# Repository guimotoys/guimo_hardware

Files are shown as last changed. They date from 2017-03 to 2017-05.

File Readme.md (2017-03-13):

N|Solid (https://guimo.toys)
# [Guimo&trade;] Hardware Sources

## What is Guimo&trade;?
[Guimo&trade;] is a modular smart toy, created to inspire children to live out-of-this-world experiences! It is a being from another planet, who was on an intergallactic mission when was hit by a meteor and fell on the Earth, losing parts of its pieces, programming and personality. The children's goal is to help [Guimo&trade;] recover its programming and mold its personality, by using our free app on a tablet or compatible smartphone.

N|Solid (https://guimo.toys) N|Solid (https://guimo.toys) 

## What is the [Guimo&trade;] Hardware Sources?   

Aqui na pasta de Hardware existe uma lista de todos os componentes necessários para se fazer um Guimo. Essa lista chama-se BOM-Guimo, sinta-se à vontade para baixá-la e adicionar componentes que possam ser compatíveis.

Além disso, há um arquivo com o esquemático da placa do Core. Faça o download e exporte o arquivo da PCB em PDF para posteriormente imprimí-lo e fazer sua própria placa caseira do guimo.
Abaixo segue um tutorial de como fazer sua própria PCB caseira e os materiais necessários:
http://www.robsonmartins.com/eletr/transfterm/

* Observação:
Na hora de fazer a impressão do seu PDF, deve-se atentar-se à orientação da imagem, pois a mesma deve estar invertida como um espelho do circuito final desejado.

## License
Copyright CERN 2013.

This documentation describes Open Hardware and is licensed under the CERN OHL v. 1.2.

You may redistribute and modify this documentation under the terms of the CERN OHL v.1.2. (http://ohwr.org/cernohl). This documentation is distributed WITHOUT ANY EXPRESS OR IMPLIED WARRANTY, INCLUDING OF 
MERCHANTABILITY, SATISFACTORY QUALITY AND FITNESS FOR A PARTICULAR PURPOSE. Please see the CERN OHL v.1.2 for applicable conditions

[Guimo&trade;]: <https://guimo.toys>

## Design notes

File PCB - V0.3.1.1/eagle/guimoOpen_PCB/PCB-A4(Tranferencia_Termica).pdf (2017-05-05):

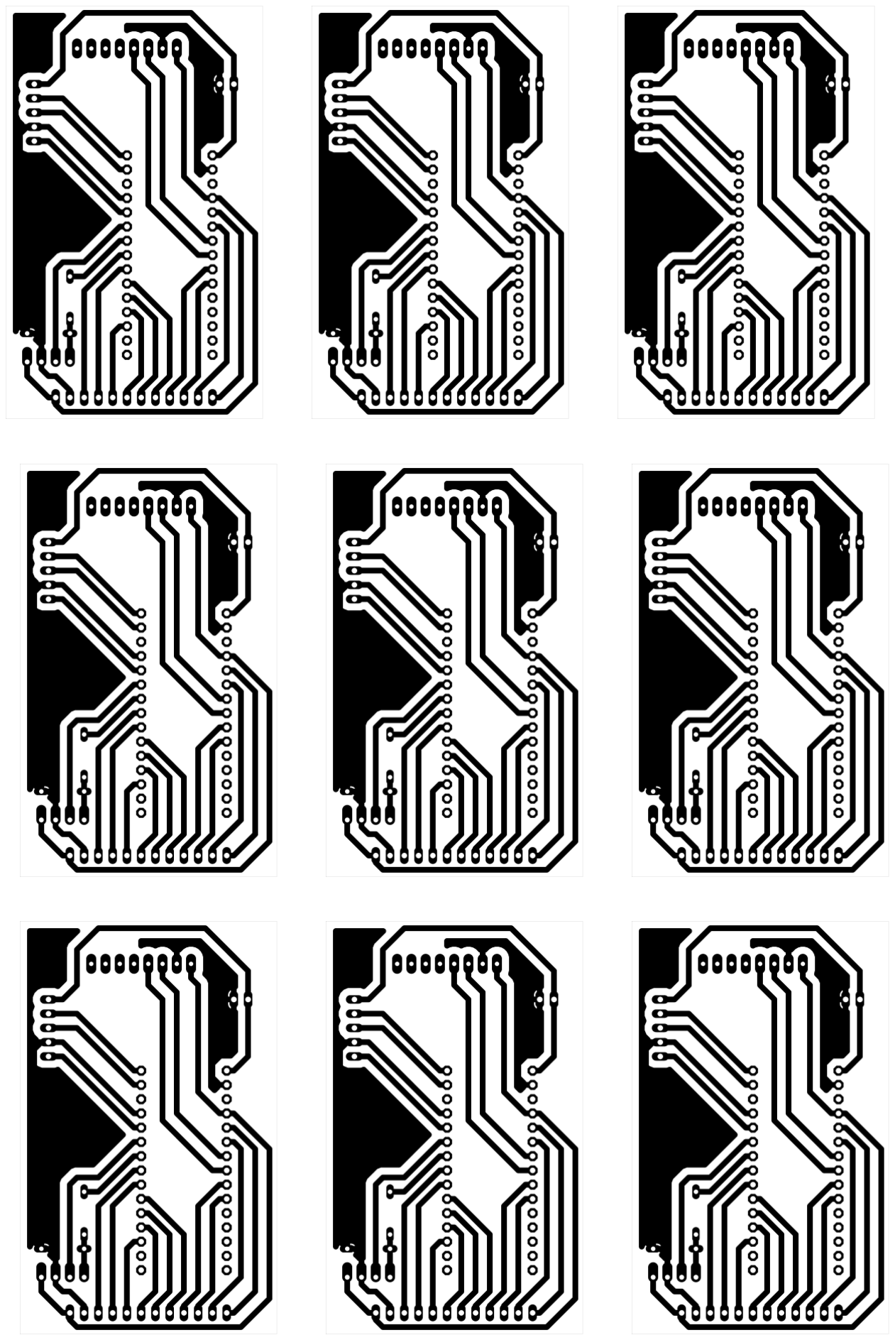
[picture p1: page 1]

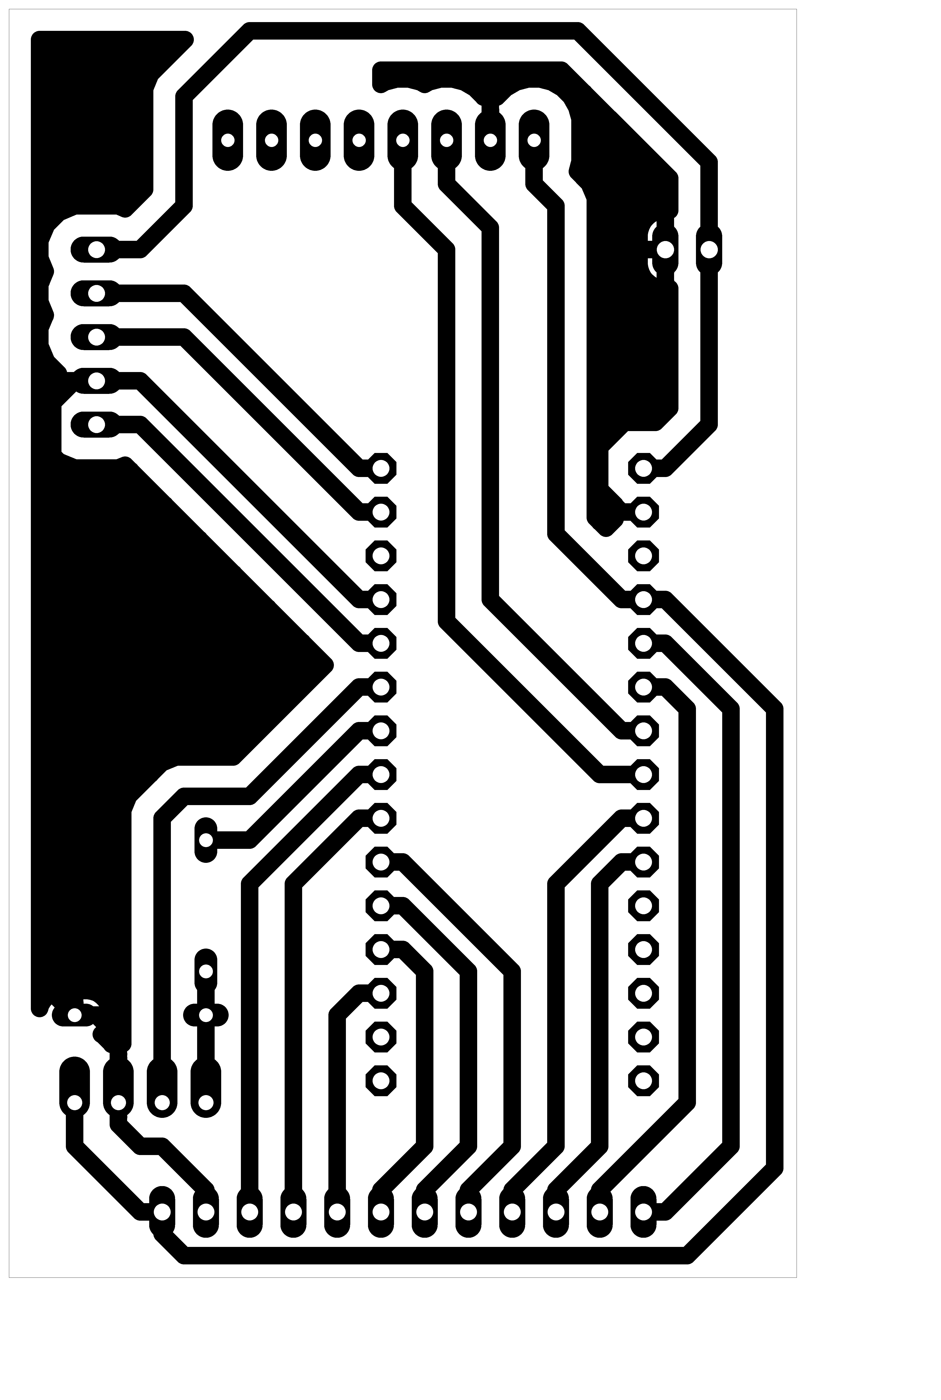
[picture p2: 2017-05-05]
PCB - V0.3.1.1/eagle/guimoOpen_PCB/Fotolito_GuimoV0311(Transferencia_Termica).png

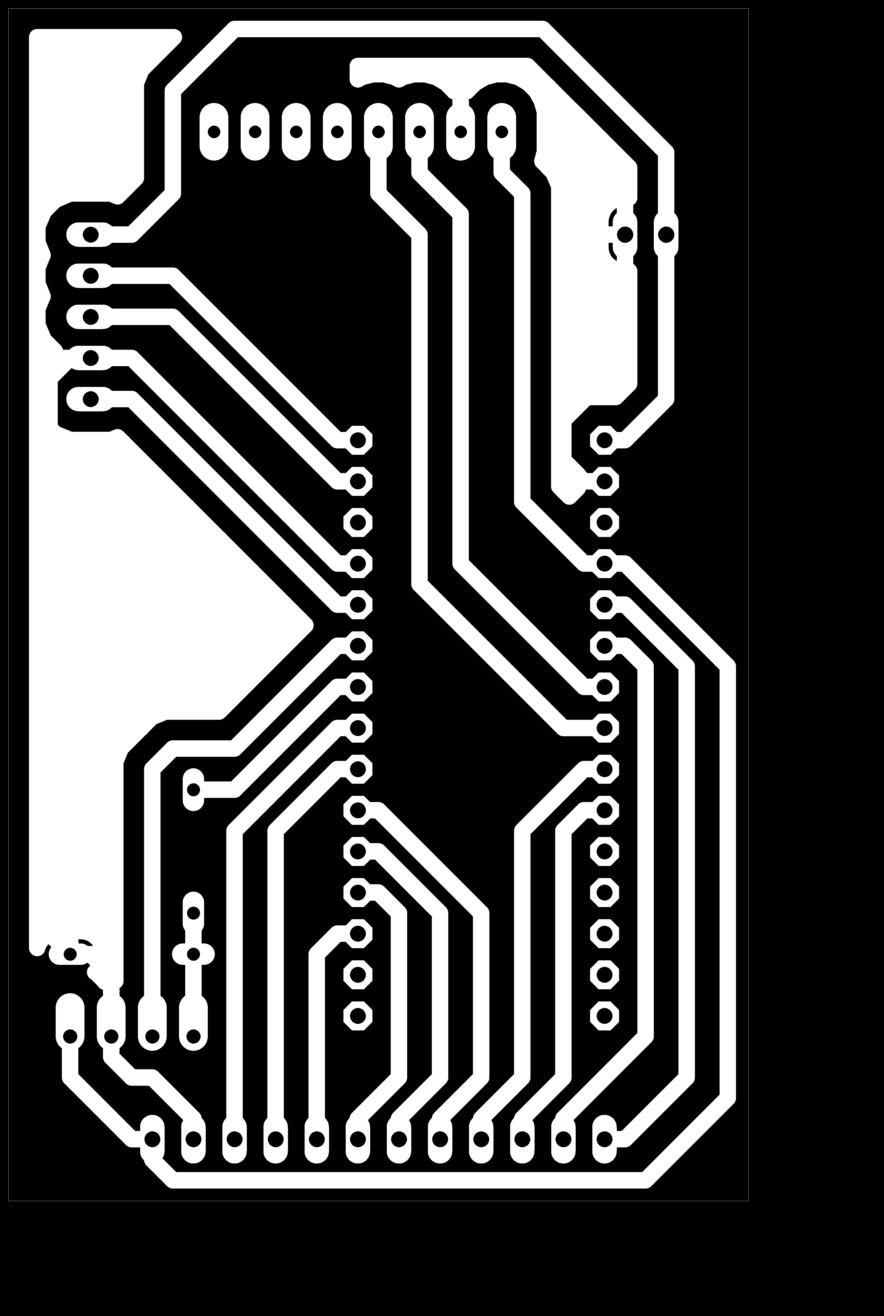
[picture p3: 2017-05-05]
PCB - V0.3.1.1/eagle/guimoOpen_PCB/Fotolito_GuimoV0311(Ultravioleta).png

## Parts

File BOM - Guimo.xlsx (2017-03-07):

 | Quantidade | Código | Nome | Descrição | Fabricante | Número do Fabricante | Preço Unitário (R$) | Preço Total (R$)
Placa Core | 1 | PUR031-C001 | Arduino Nano | ATmega328 Arduino Nano AVR® ATmega MCU 8-Bit AVR Embedded Evaluation Board | Arduino | A000005 | R$49.90 | R$ 49.90
 | 1 | PUR031-C002 | Acelerômetro e Giroscópio | Gy521 Mpu-6050 Module, Axis Gyroscope Module, Accelerometer Module manufacturer / supplier in China, offering Gy-521 Mpu-6050 3 Axis Gyroscope and Accelerometer Module, Wrobot Digital 38kHz IR Transmitter Sensor Arduino Compatible, Serial Port Bluetooth with Baseboardslave Arduino Compatible and so on. | Shanhai | GY521 MPU-6050 Module | R$22.90 | R$ 22.90
 | 1 | PUR031-C003 | Bluetooth | Módulo Bluetooth RS232 HC-05 |  |  | R$36.90 | R$ 36.90
 | 2 | PUR031-C004 | Barra de 15 pinos | 15 Position Header Connector 0.100" (2.54mm) Through Hole Tin | Sullins Connector Solutions | PPTC151LFBN-RC | R$1.09 | R$ 2.18
 | 1 | PUR031-C005 | Barra de 12 pinos | 12 Position Header Connector 0.100" (2.54mm) Through Hole Tin | Sullins Connector Solutions | PPTC121LFBN-RC | R$0.87 | R$ 0.87
 | 1 | PUR031-C006 | Barra de 6 pinos | 6 Position Header Connector 0.100" (2.54mm) Through Hole Tin | Sullins Connector Solutions | PPTC061LFBN-RC | R$0.43 | R$ 0.44
 | 1 | PUR031-C007 | Barra de 5 pinos | 5 Position Header Connector 0.100" (2.54mm) Through Hole Tin | Sullins Connector Solutions | PPTC051LFBN-RC | R$0.36 | R$ 0.36
 | 1 | PUR031-C008 | Barra de 8 pinos | 8 Position Header Connector 0.100" (2.54mm) Through Hole Tin | Sullins Connector Solutions | PPTC081LFBN-RC | R$0.58 | R$ 0.58
 | 1 | PUR031-C009 | Barra de 2 pinos | 2 Positions Header, Breakaway Connector 0.100" (2.54mm) Through Hole Gold | Sullins Connector Solutions | PRPC002SAAN-RC | R$0.07 | R$ 0.07
 | 2 | PUR031-C010 | Resistor | 220 Ohm ±5% 0.25W, 1/4W Through Hole Resistor Axial Flame Retardant Coating, Safety Carbon Film | Stackpole Electronics Inc. | CF14JT220R | R$0.10 | R$ 0.19
Head | 1 | PUR031-H001 | Arduino UNO | ATmega328P Arduino Uno AVR® ATmega MCU 8-Bit AVR Embedded Evaluation Board | Arduino | A000066 | R$49.90 | R$ 49.90
 | 1 | PUR031-H002 | TFT LCD | 2.4'' TFT LCD Shield Arduino ILI9341 | mcufriend | C202 | R$69.90 | R$ 69.90
 | 1 | PUR031-H003 | Cartão Micro SD | Memory Card microSD™ 8GB Class 10 MLC | ATP Electronics, Inc. | AF8GUD3-OEM | R$34.90 | R$ 34.90
 | 1 | PUR031-H004 | Sensor de Toque | Sensor Touch Capacitivo TTP223B |  |  | R$16.90 | R$ 16.90
Body | 2 | PUR031-B001 | Micro Servo Motor | Micro Servo 9g SG90 TowerPro, Peso 9g, Dimensão 23x12.2x29mm, Torque 1.8Kg/cm(4.8V), Tensão de operação: 4.8V, Temperatuda de Operação: 0-55ºC | TowerPro | SG90 | R$14.90 | R$ 29.80

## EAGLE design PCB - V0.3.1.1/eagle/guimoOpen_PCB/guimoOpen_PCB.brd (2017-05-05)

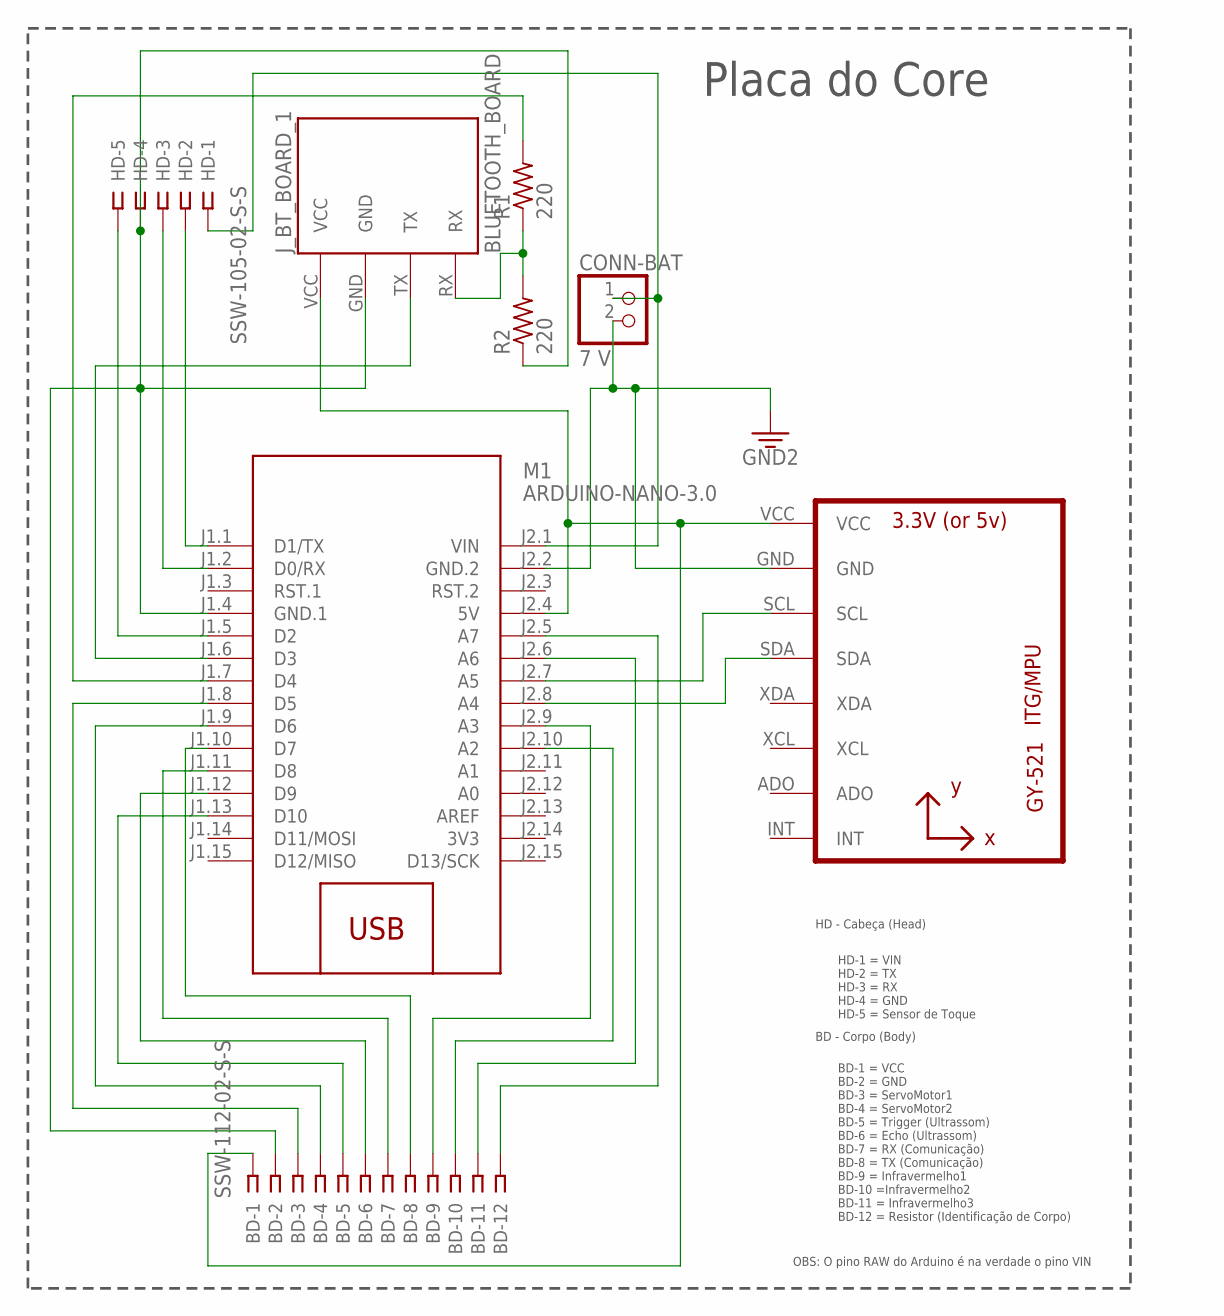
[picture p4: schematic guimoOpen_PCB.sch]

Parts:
BD: SSW-112-02-S-S
CONN-BAT: 7 V; 1X02
HD: SSW-105-02-S-S
J_BT_BOARD_1: BLUETOOTH_BOARD; BT_BOARD_FOOTPRINT
M1: ARDUINO-NANO-3.0
R1, R2: 220; 0207/7
U1: GY-521MPU6050; GY-521

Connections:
3V3: M1.J2.14 (3V3)
GND: BD.2, HD.4, J_BT_BOARD_1.GND, M1.J1.4 (GND.1), R2.1
GND1: CONN-BAT.2, M1.J2.2 (GND.2), U1.GND
unnamed: J_BT_BOARD_1.RX, R1.1, R2.2
unnamed: BD.1, J_BT_BOARD_1.VCC, M1.J2.4 (5V), U1.VCC
unnamed: M1.J2.7 (A5), U1.SCL
unnamed: M1.J2.8 (A4), U1.SDA
unnamed: HD.5, M1.J1.5 (D2)
unnamed: CONN-BAT.1, HD.1, M1.J2.1 (VIN)
unnamed: M1.J1.7 (D4), R1.2
unnamed: BD.4, M1.J1.9 (D6)
unnamed: BD.6, M1.J1.12 (D9)
unnamed: BD.7, M1.J1.11 (D8)
unnamed: BD.5, M1.J1.13 (D10)
unnamed: BD.3, M1.J1.8 (D5)
unnamed: BD.8, M1.J1.10 (D7)
unnamed: BD.12, M1.J2.5 (A7)
unnamed: BD.11, M1.J2.6 (A6)
unnamed: J_BT_BOARD_1.TX, M1.J1.6 (D3)
unnamed: HD.2, M1.J1.1 (D1/TX)
unnamed: BD.9, M1.J2.9 (A3)
unnamed: BD.10, M1.J2.10 (A2)
unnamed: HD.3, M1.J1.2 (D0/RX)

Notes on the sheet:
Placa do Core
BD-1 = VCC BD-2 = GND BD-3 = ServoMotor1 BD-4 = ServoMotor2 BD-5 = Trigger (Ultrassom) BD-6 = Echo (Ultrassom) BD-7 = RX (Comunicação) BD-8 = TX (Comunicação) BD-9 = Infravermelho1 BD-10 =Infravermelho2 BD-11 = Infravermelho3 BD-12 = Resistor (Identificação de Corpo)
HD-1 = VIN HD-2 = TX HD-3 = RX HD-4 = GND HD-5 = Sensor de Toque
HD - Cabeça (Head)
BD - Corpo (Body)
OBS: O pino RAW do Arduino é na verdade o pino VIN

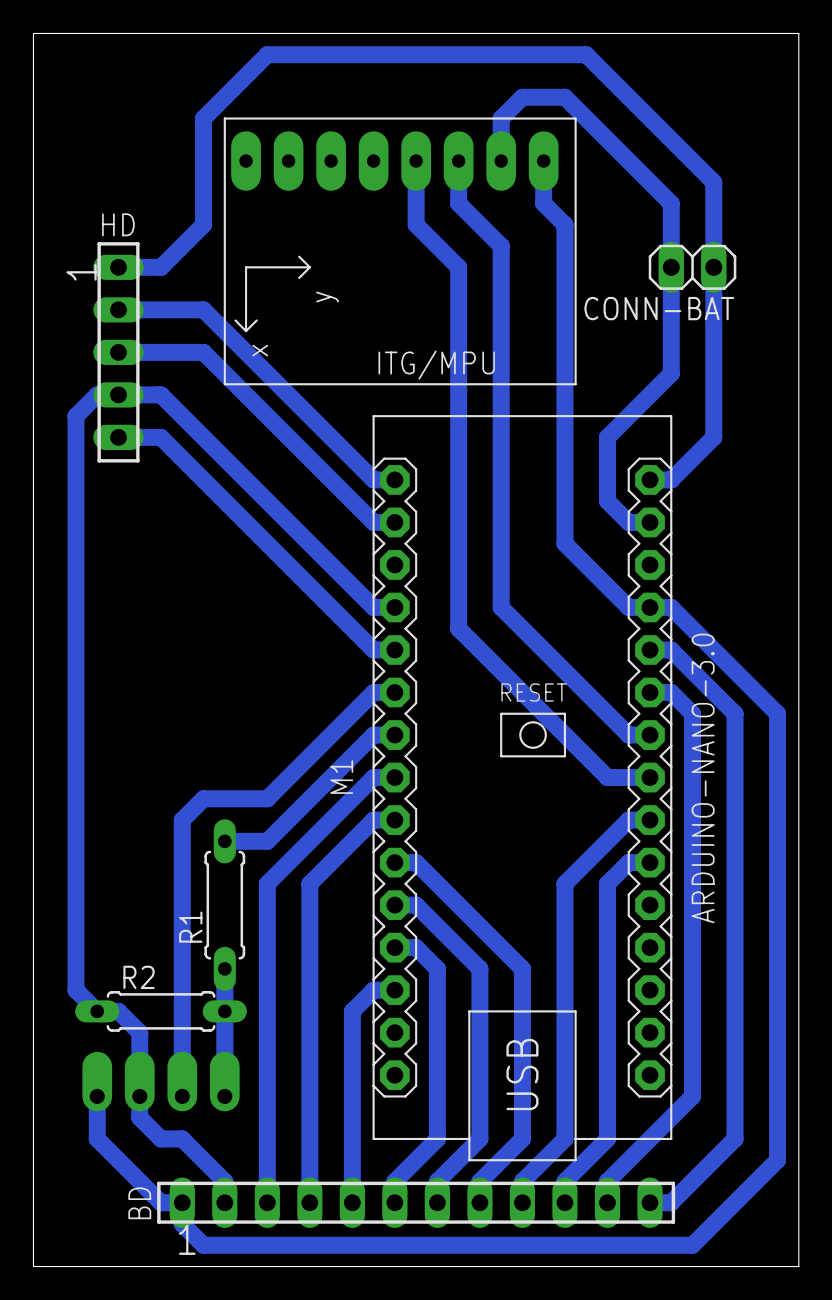
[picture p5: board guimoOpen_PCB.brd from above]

Board: 2 copper layers, 45.7 x 73.7 mm, 8 parts (1 on the bottom side), 22 nets.

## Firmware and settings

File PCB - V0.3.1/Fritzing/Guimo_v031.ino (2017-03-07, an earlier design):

#include <Arduino.h>

// Descrição das Portas Utilizadas
// Digitais: 2,3,5,6,7
// Analógicas: 
// Por Periférico: Ultrassom(D2,D3); Bluetooh(D5,D6); ResistorCorpo(D7); Motores(D10,D11);   

#include <SoftwareSerial.h>
#include<Wire.h>
#include<Servo.h>

#define echoPin 2
#define trigPin 3

char bufB;  //Buffer de comunicação do Bluetooh
char buf;  //Buffer de comunicação com a Cabeça (arduino com arduino)
const int MPU=0x68;  
int AcX,AcY,AcZ; 
int corpo = 7;
int val = 0;
int pinoSensor = A6;
int valorSensor = 0;
long randNumber;

Servo motorDireita, motorEsquerda;

// Define os pinos para a serial  (RX, TX)
SoftwareSerial MinhaSerial(6,5);

void setup() {
  pinMode(trigPin, OUTPUT);
  pinMode(echoPin, INPUT);
  pinMode(corpo, INPUT);

  //Inicia a serial 
  Serial.begin(9600); 
  Serial.println("Dados recebidos :"); 
  
  MinhaSerial.begin(9600);
 
  Wire.begin();
  Wire.beginTransmission(MPU);
  Wire.write(0x6B); 
   
  //Inicializa o MPU-6050
  Wire.write(0); 
  Wire.endTransmission(true);

} 
    
void loop() 
{     
  val = digitalRead(corpo);
  if (val > 0)
  {
    MinhaSerial.println("carrinho");
  }

  buf = Serial.read();

  if (buf == '1')
  {
    MinhaSerial.println("guimo");
  }

  if (buf == '2')
  {
    MinhaSerial.println("robo");
  }
  
// Ações Bluetooh
//------------------------------------------------------------------  
  while(MinhaSerial.available() > 0)
  {
    bufB = MinhaSerial.read();
    
// Troca de tela
    if (bufB == 'g')
    {
      MinhaSerial.println("g");
      Serial.println("g");
    }
    
    if (bufB == 'a')
    {
      acelerometro();
    }
    
// Programação para controlar os movimentos do Guimo   
    if (bufB == 'f')
    {
      MinhaSerial.println("Avante GUIMO");
      Serial.println("Avante GUIMO");
      rotacao_Frente();
      while(MinhaSerial.available() > 0)
      bufB = MinhaSerial.read();
    }
    
    if (bufB == 'l')
    {
      MinhaSerial.println("Esquerda");
      Serial.println("Esquerda");
      rotacao_Esquerda();
      while(MinhaSerial.available() > 0)
      bufB = MinhaSerial.read();
    }
    
    if (bufB == 'r')
    {
      MinhaSerial.println("Direita");
      Serial.println("Direita");
      rotacao_Direita();
      while(MinhaSerial.available() > 0)
      bufB = MinhaSerial.read();
    }
    
    if (bufB == 'b')
    {
      MinhaSerial.println("Tras");
      Serial.println("Tras");
      rotacao_Re();
      while(MinhaSerial.available() > 0)
      bufB = MinhaSerial.read();
    }

// A função Autônomo só começará quando o Guimo receber "u"
    if (bufB == 'u')
    {
      guimo_Autonomo();
    }

// A função Segue-linha só começará quando o Guimo receber "s"
//    if (bufB == 's')
//    {
//      valorSensor = analogRead(pinoSensor);
//      if (valorSensor > 50)
//      {
//        segue_Linha();
//        Serial.println("Linha Detectada");
//        delay(1000);
//      }
//    }
  }
}
//------------------------------------------------------------------


// Reinicia o programa do início, mas não reseta os periféricos e os registros
void software_Reset() 
{
  asm volatile ("jmp 0");
}  

// Função para o Guimo seguir uma linha
//void segue_Linha() {
//  if (valorSensor > 50){
//    rotacao_Frente();
//  }
//  
//}

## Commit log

2017-01-29 Programas corretos do Core. Recebendo e enviando os códigos de imagem BMP
2017-01-29 Apaguei a outra versão, pois não era o programa correto e mais recente que está rodando no Guimo
2017-01-29 Acrescentei o código do acelerômetro para identificar quando o Guimo está de ponta-cabeça
2017-03-07 Projetos da PCB Versão 0.3.1
    [Guimo_0-3-1.fzz, PCB_Guimo_0-3-1.fzz]
2017-03-07 Atualização do diretório PCB
    [Guimo_0-3-1.fzz, PCB_Guimo_0-3-1.fzz]
2017-03-07 Apaguei os programas da pasta guimo_hardware e os realoquei para a pasta guimo_firmware
2017-03-07 Novo layout da PCB com o programa Fritzing com alguns problemas corrigidos (divisor de tensão e alimentação 5V do corpo)
    [Guimo_0-3-1-1.fzz]
2017-03-07 Bill Of Materials do Guimo - Primeira versão
    [BOM - Guimo.xlsx]
2017-03-13 Nova PCB do Guimo no software Eagle. Pendente de teste.
    [guimoOpen_PCB.brd, guimoOpen_PCB.sch]
2017-03-19 Imagens para impressão da placa PCB corrigidas
2017-05-05 Correção do roteamento do acelerômetro. SDA e SCL foram colocadas nas portas A4 e A5
    [guimoOpen_PCB.brd, guimoOpen_PCB.sch]

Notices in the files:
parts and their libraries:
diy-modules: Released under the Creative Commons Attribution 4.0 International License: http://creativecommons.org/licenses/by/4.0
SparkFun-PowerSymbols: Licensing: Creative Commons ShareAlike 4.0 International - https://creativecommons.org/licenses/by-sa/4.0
